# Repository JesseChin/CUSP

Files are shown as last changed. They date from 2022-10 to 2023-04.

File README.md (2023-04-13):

# CUSP

[github link](https://github.com/JesseChin/CUSP)

[User Guide](https://github.com/JesseChin/CUSP/blob/main/docs/User%20Guide.docx)

## Project Description

The Compact UAV Sensor Package (CUSP) is a low-cost camera sensor package with a longwave infrared (LWIR, 8 μm to 14 μm) and a high-resolution RGB camera for use with UAV remote sensing. The package is being developed as part of NASA Land Cover and Land Use Change and Ecosystems priority topic for NASA SERVIR-WA (West Africa) and for the Center for Remote Sensing and Geographic Information Services (CERSGIS), collaborating with the Environmental Protection Agency in Ghana. The purpose of these sensors is to combat deforestation and land degradation by monitoring illegal charcoal production and Galamsey operations (illegal small-scale gold mining). A machine learning model will be created to recognize these sites and report to the operator live.

CUSP is a unique low cost and lightweight product that provides on-board Machine Learning processing, a simple web configuration portal, and is fully open-source. Existing commercial solutions which provide live on-board image recognition do exist, though they are not open-source and certainly not budget-friendly. Existing open-source implementations, such as Imaging Package for Remote Vehicles (imPROV) do not provide ML capabilities, rely on 4G to operate, and occupy a large volume. CUSP is the only low-cost, small, and open-source sensor capable of monitoring illegal charcoal production and Galamsey.

---
## Screenshots

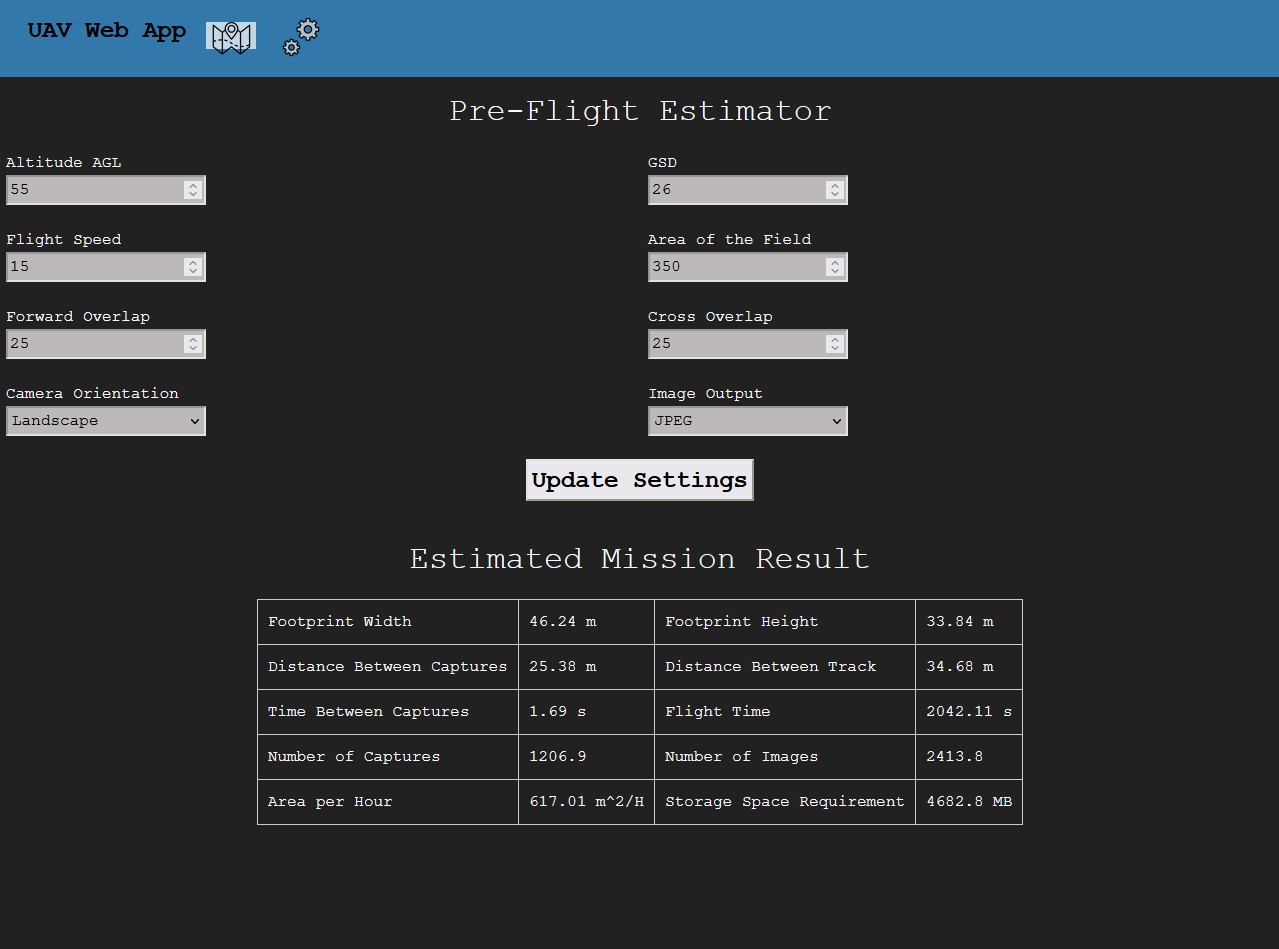
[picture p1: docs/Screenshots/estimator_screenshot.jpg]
estimator_screenshot


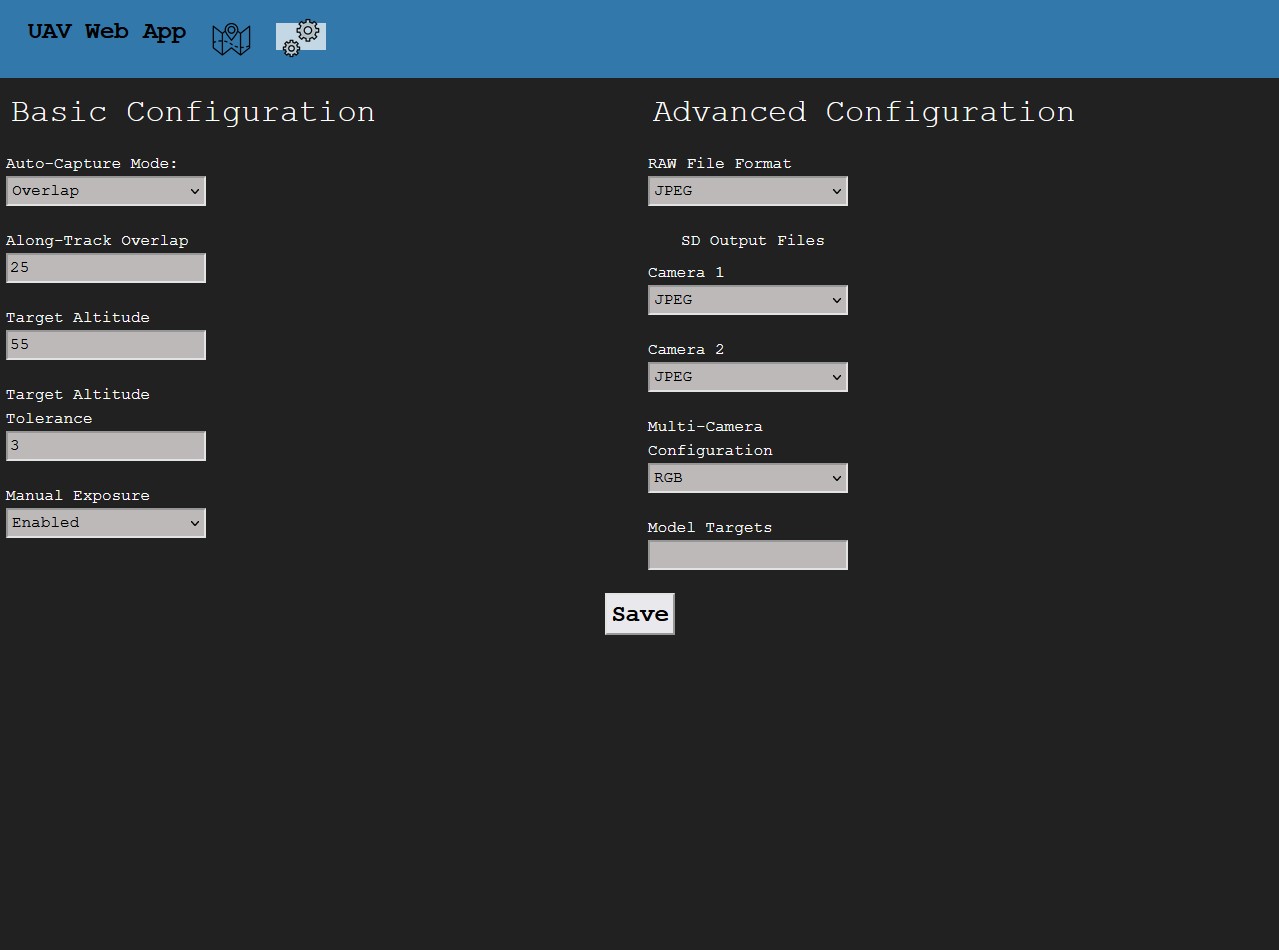
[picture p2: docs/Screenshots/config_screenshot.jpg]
config_screenshot


---
## Requirements

### Hardware
- Raspberry Pi 3/4
- MAVLink Capable Flight Controller
- 15-pin Raspberry Pi Compatible Camera
- FLIR Lepton Thermal Imaging Sensor
- CUSP Pi Hat
- 3D printed Chassis
- 4x M2.5x20 screws
- 9x M2.5x6 screws
- 4x M2x6 screws

### Software
- Python 3.9.2+
- Pymavlink
- Flask

---
## System Diagram

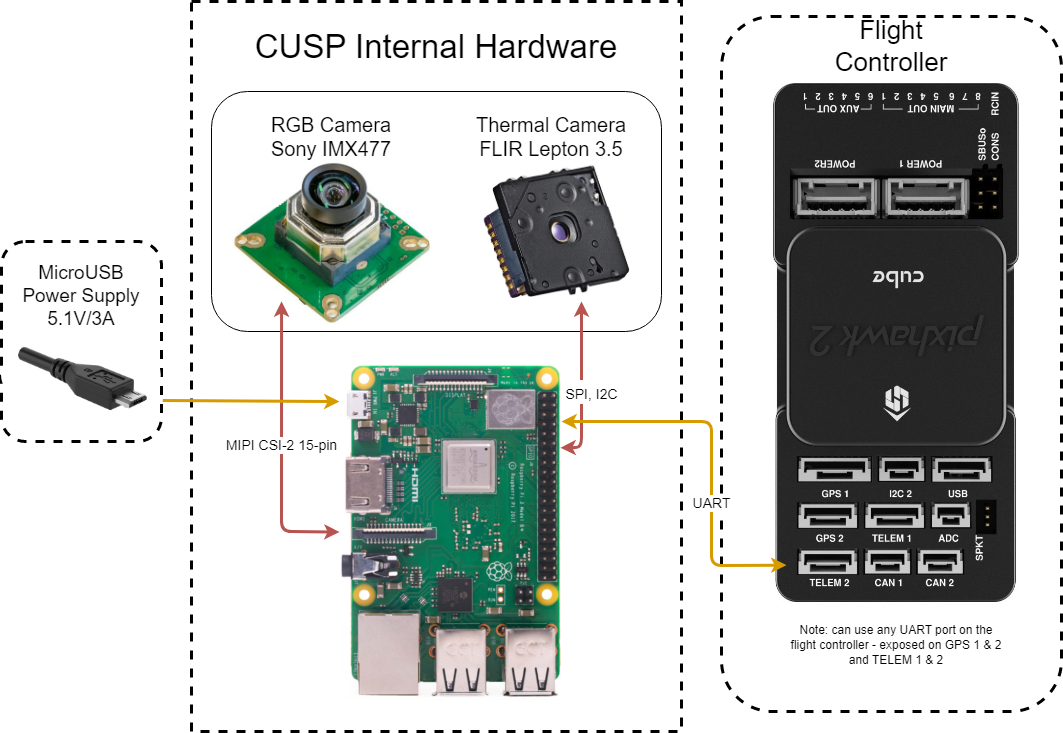
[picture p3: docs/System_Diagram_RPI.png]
System Diagram


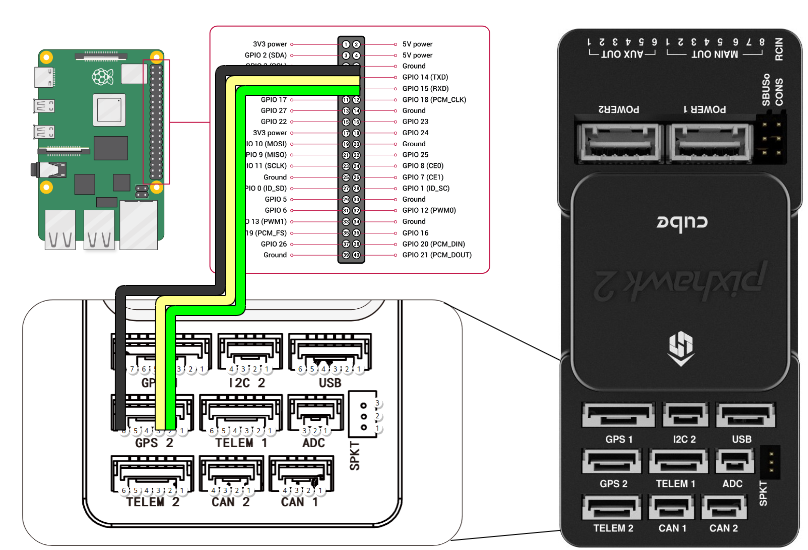
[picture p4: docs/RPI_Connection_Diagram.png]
Raspberry Pi <---> Flight Control


---
## Component Explanation

`MAVLINK_Camera` is a folder containing test scripts intended to run on the raspberry pi. `get_params_test.py` and `mavlink_test.py` tests the MAVLink connection and `camera_get.py` tests the attached camera. `CUSP_camera.py` is the camera capturing module, `CUSP_error_types.py` is the error type module, `CUSP_gps.py` is the gps handling module, `CUSP_messages.py` is the module containing our message enumerations, `CUSP_trigger.py` is the moduel containing logic for specific event triggers, and finally `main.py` is the application stating point.

captured images are saved in the `$HOME/data` directory on the pi.

The `Web_App` folder contains all the files needed to host the web server on the Raspberry Pi. The server is written in Python with Flask and HTML+CSS. the static folder contains all the assets and the templates folder contains all the html files. `app.py` is the starting point.

The `docs` folder will contain any extra documentation as the project develops. For example, `gcs_test_msg.PNG` and `gcs_test_msg1.PNG` show that `mavlink_test.py` is functional.

The `sim` folder contains all our files to help simualte a flight controller in flight so we do not need to actually fly a drone to develop new featues. Does not require running on hardware, can be fully simulated directly on a development machine. [This README](sim/README.md) contains much more info.

The `pi_sim` folder contains a mocked implementation of the GPS module and supports SITL running directly on the Pi for simulating a flight without actually flying the drone. The camera capturing mode here is fully implemented. This is where most of our development occurs.

### Persistent State

Camera capturing configuration parameters are stored in `$HOME/Web_App/form_data.json`. This json file contains the parameters for target altitude, target altitude tolerance, capturing mode (trigger, overlap, PWM), and output modes (JPEG, TIFF). Upon startup of the main application (`main.py`), this json is read. In the event of power loss, the camera configuration data is still held.

Images are saved into the `$HOME/images/` directory. Images are saved in the format YYYY_MM_DD_HH_MM_SS_{RGB, IR}. Currently, we are saving the IR images in RAW format for further radiometric processing.

---
## Setup
To use the Lepton sensor we needed to modify the kernel of the Pi. [This guide](https://github.com/FLIR/Lepton/blob/main/docs/RaspberryPiGuide.md) worked for us.

MAVProxy is a convenient way to test the connection of the Pi and flight controller. It also installs pymavlink as a dependency:
```
sudo apt-get install python3-dev python3-opencv python3-wxgtk4.0 python3-pip python3-matplotlib python3-lxml python3-pygame
pip3 install PyYAML mavproxy --user
echo 'export PATH="$PATH:$HOME/.local/bin"' >> ~/.bashrc
```

```
sudo apt install libimage-exiftool-perl libcamera
pip install PyExifTool
```

For autostarting the program:
```
sudo cp scripts/* /etc/systemd/system/
sudo systemctl enable cusp-main.service
sudo systemctl start cusp-main.service
sudo systemctl enable cusp-web.service
sudo systemctl start cusp-web.service
```

After that, installing Flask is simple:

```
pip install Flask flask-wtf flask-reuploaded
```

Now make sure the system is wired as shown in the [System Diagram](#System-Diagram), and you should be able to run our test scripts.

## Usage

to start the web server connect to the pi via SSH, navigate to the Web_App folder, and run the following command:

```
flask run --host=<ip_address>
```

Alternatively, the web server can also be called via `./scripts/run_webserver.sh`. This script automatically determines the ip of the pi.

where `<ip_address>` is replaced with the Pi's current ip address.

Once this is running you will be able to access the web interface through any web browser (we tested both Chrome and Firefox) by typing `http://<ip_address>:5000` into the address bar, once again replacing `<ip_address>` with the Pi's current ip address.

This whole process will hopefully be made much more user friendly in upcoming builds.

At this point there are two useful tabs, both of which can be accessed with the icons on the navigation bar on the top of the screen.

The first is the Pre-Flight Estimator. This tab allows the user to estimate the stats of a flight using already known variables. To learn the units of each variable, simply hover your mouse over it. When the user is ready they can select the large "Update Settings" button and they will either be greeted with an appropriate error message or the result of their flight.

The next useful tab is the Configuration Menu. This is where the data is configured for the actual flight. Once this data is filled the user can select the "Save" button, at which point they will receive a notification containing an appropriate error message or "JSON Saved"

We are using systemd services to run CUSP as a background process. Systemd supports automatically starting programs upon an operating system hook (i.e., network daemon activated) and restarting when an error occurs. If the systemd services are active, the main program and webserver should launch automatically on startup. Upon crash of either program, systemd should wait 5 seconds and auto-restart the service.

### Manual flight with pi_sim
pi_sim requires a connection to SITL. Because DroneKit-SITL does not have ARM builds, ardupilot SITL must be built manually using the [ArduPilot Building Guide](https://github.com/ArduPilot/ardupilot/blob/master/BUILD.md).

To begin a flight simulation, run the steps in [the sim README](sim/README.md).
After launching SITL, navigate to the pi_sim folder and run the following command:

```
python3 main.py
```

Now, images will be automatically captured dependent on the camera configuration. For example, if trigger capturing mode is enabled with a period of 10s, RGB and IR images will be captured every 10 seconds.

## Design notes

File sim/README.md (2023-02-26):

# Software Simulator

Software In The Loop (SITL) is a simulator that allows running ArduPilot without hardware. Using this, we are able to simulate running CUSP without having to connect to the flight controller and cameras.

There are two ways of running SITL: with the official ArduPilot codebase or using DroneKit-SITL. DroneKit-SITL does not have as many pre-built vehicles, but is significantly easier to install and run. In this project, we will be using DroneKit-SITL.

https://ardupilot.org/dev/docs/sitl-simulator-software-in-the-loop.html
https://dronekit-python.readthedocs.io/en/latest/develop/sitl_setup.html

To install DroneKit-SITL:
`pip install dronekit-sitl -UI`

To run DroneKit-SITL:
`dronekit-sitl copter`
SITL starts and waits for a TCP connection at 127.0.0.1:5760

Using SITL instead of a UART connection to MAVLink is quite easy, just a drop-in replacement in the Python code.

Connection with UART on a Raspberry Pi to a Flight Controller:
```
...
    the_connection = mavutil.mavlink_connection('/dev/serial0', baud=57600, source_system=1, source_component=2)
...
```

Connection with SITL
```
...
    the_connection = mavutil.mavlink_connection('tcp:127.0.0.1:5760', baud=57600, source_system=1, source_component=2)
...
```

## Example of running a simulation

Process to manually test a simulated flight:
Activate SITL process 
```
cd ~/ardupilot/ArduCopter
../Tools/autotest/sim_vehicle.py --map --console
```
OR
```
dronekit-sitl copter --home=-35.363261,149.165230,584,353 # Can change coords
```
Connect to SITL with MAVProxy. Open a new terminal and run,
```
mavproxy.py --master tcp:127.0.0.1:5760
```
Add MAVLink output so that we can connect another application to SITL. In terminal running MAVProxy:
```
output add 127.0.0.1:14550
```
Connect to MAVProxy with our application via address udp:127.0.0.1:14550
Run flight. This simulated flight takes the drone to 40m, and flies in a 2000m circle. In MAVProxy terminal:
```
mode guided
arm throttle
takeoff 40
mode circle
param set circle_radius 2000
```

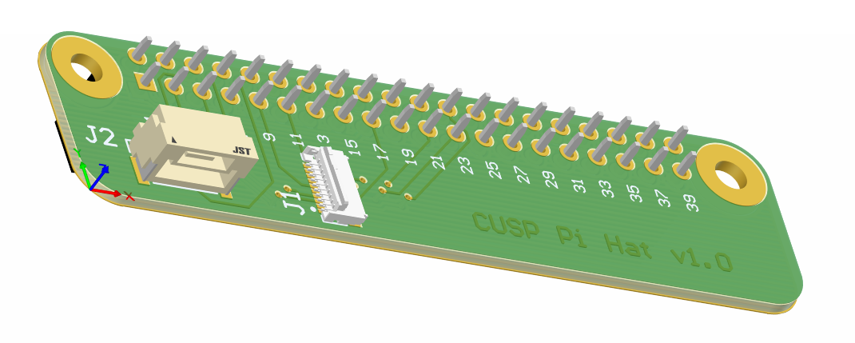
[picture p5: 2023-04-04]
hardware/Pi Hat.png

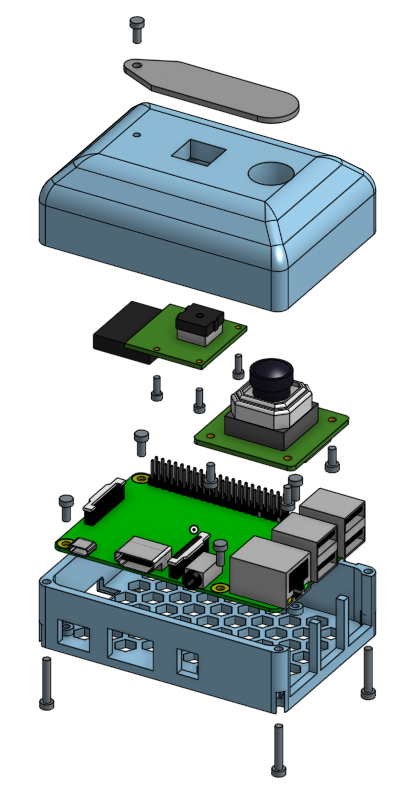
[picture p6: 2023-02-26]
hardware/explosion_view.png

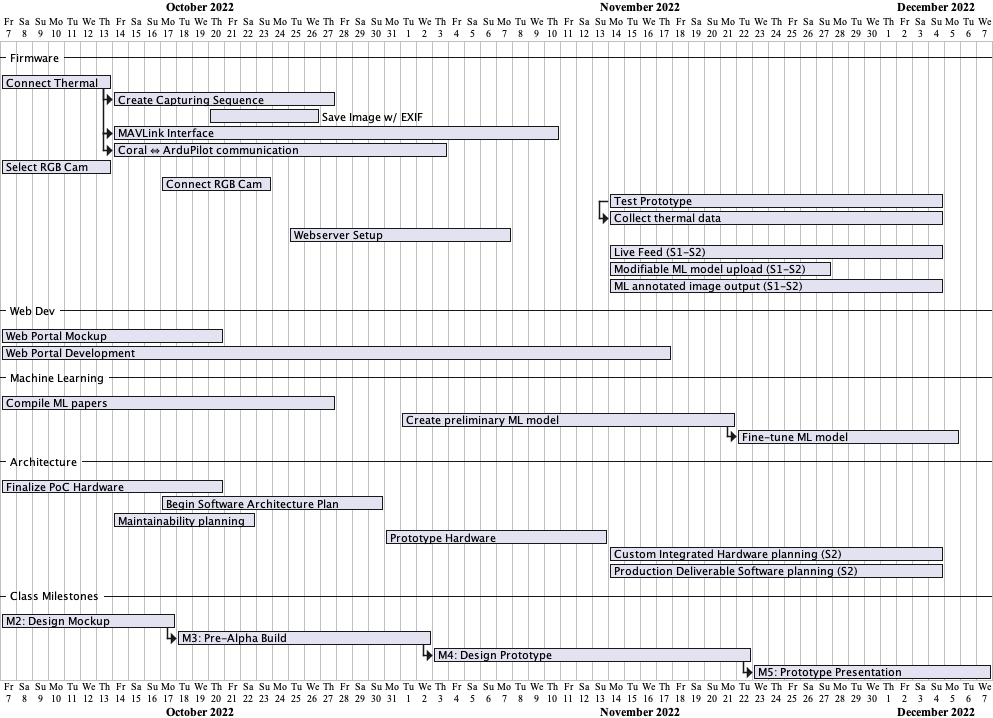
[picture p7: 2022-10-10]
out/plantuml/GanttChartSemester1/GanttChartSemester1.png

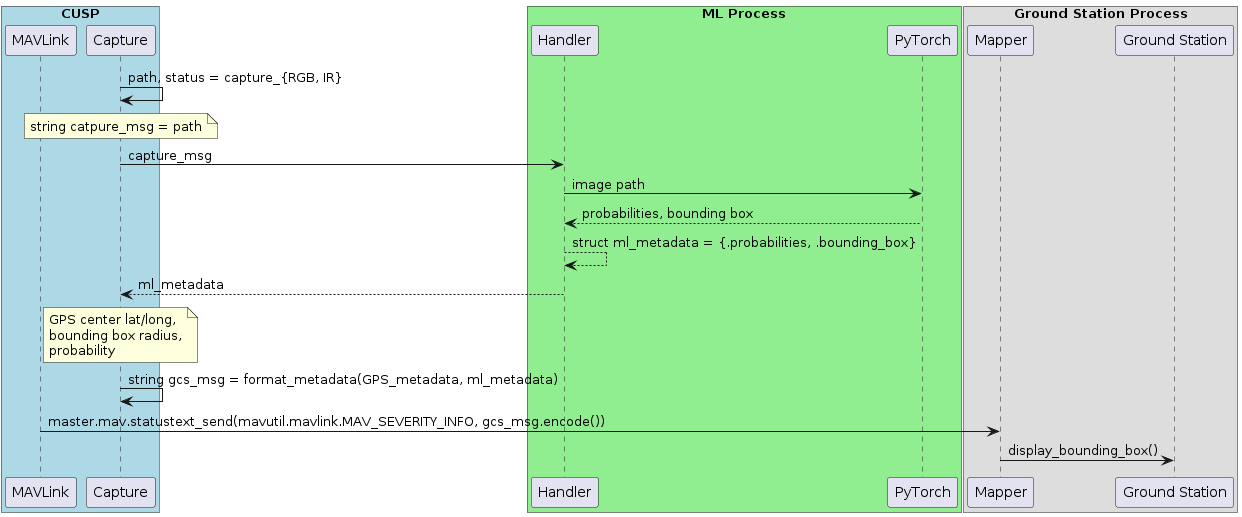
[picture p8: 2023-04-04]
out/plantuml/ML_Integration.png

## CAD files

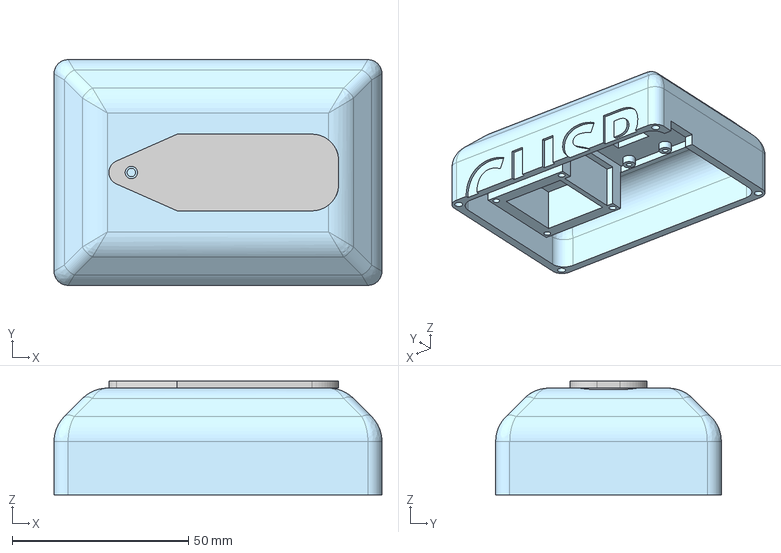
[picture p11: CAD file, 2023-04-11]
hardware/Case/Top Shell.step
93.0 x 64.0 x 32.3 mm

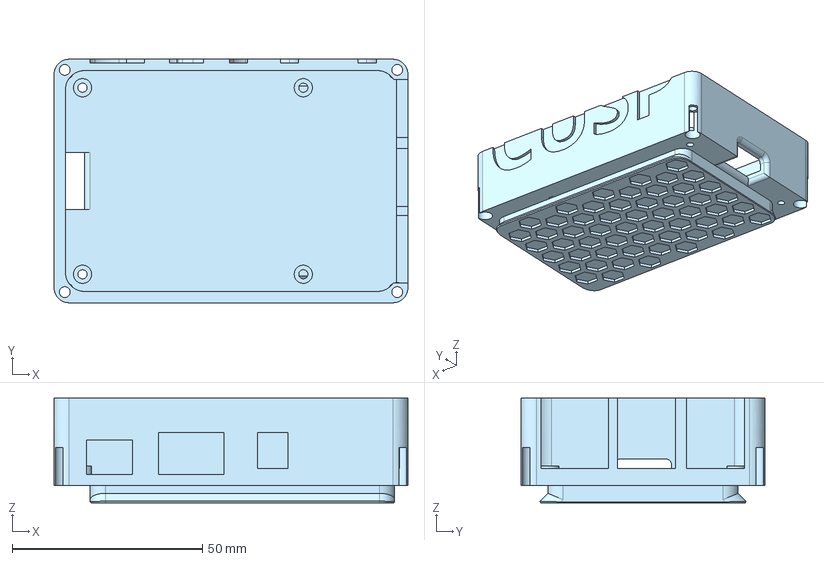
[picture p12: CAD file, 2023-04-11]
hardware/Case/Bottom Shell.step
93.0 x 64.0 x 27.5 mm

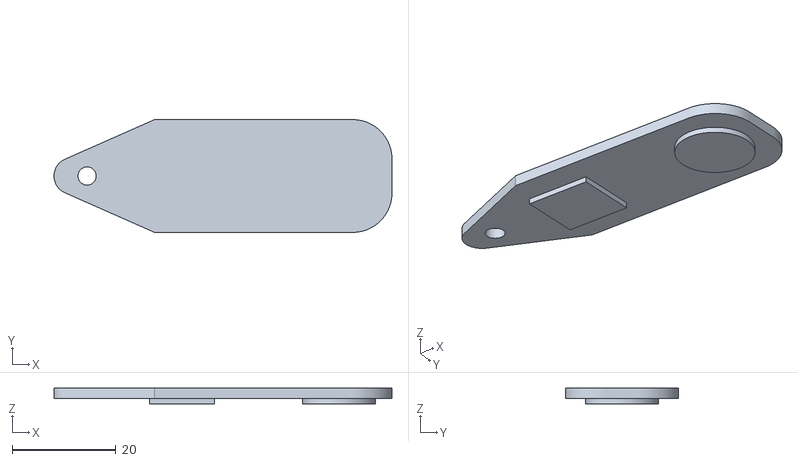
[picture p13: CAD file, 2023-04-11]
hardware/Case/Lens Cover.stl
65.2 x 21.7 x 3.00

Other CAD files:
hardware/Case/Bottom Shell.stl
hardware/Case/Top Shell.stl

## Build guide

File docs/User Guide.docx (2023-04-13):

1. Power CUSP via microUSB (or USB-C if using a RPi 4).
2. Once Cusp is powered, a wireless ad hoc network will be generated called “CUSP-XXX” where XXX will denote the unit number.
3. A user can then connect to this network just like any WiFi network using the password which is given upon arrival.
4. Upon connection, the user can now access the web app.

Web App

Go to the address 192.168.4.1:500 in a web browser.

This should bring you to the Home Page.

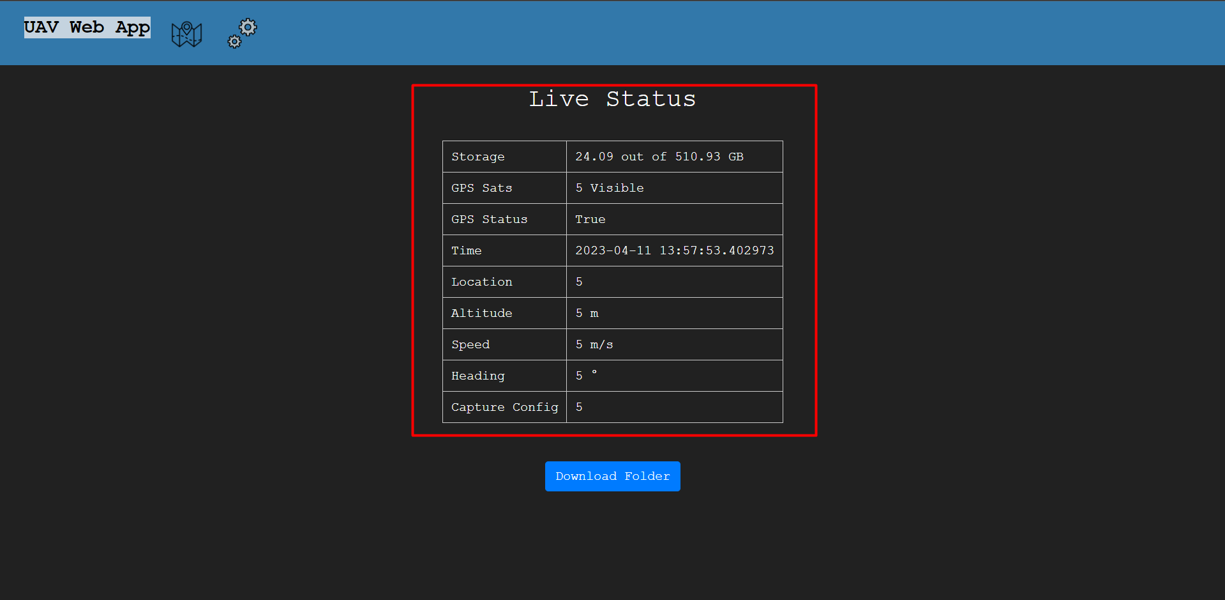
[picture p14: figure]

This part of the home page displays the status of the gps in real time.

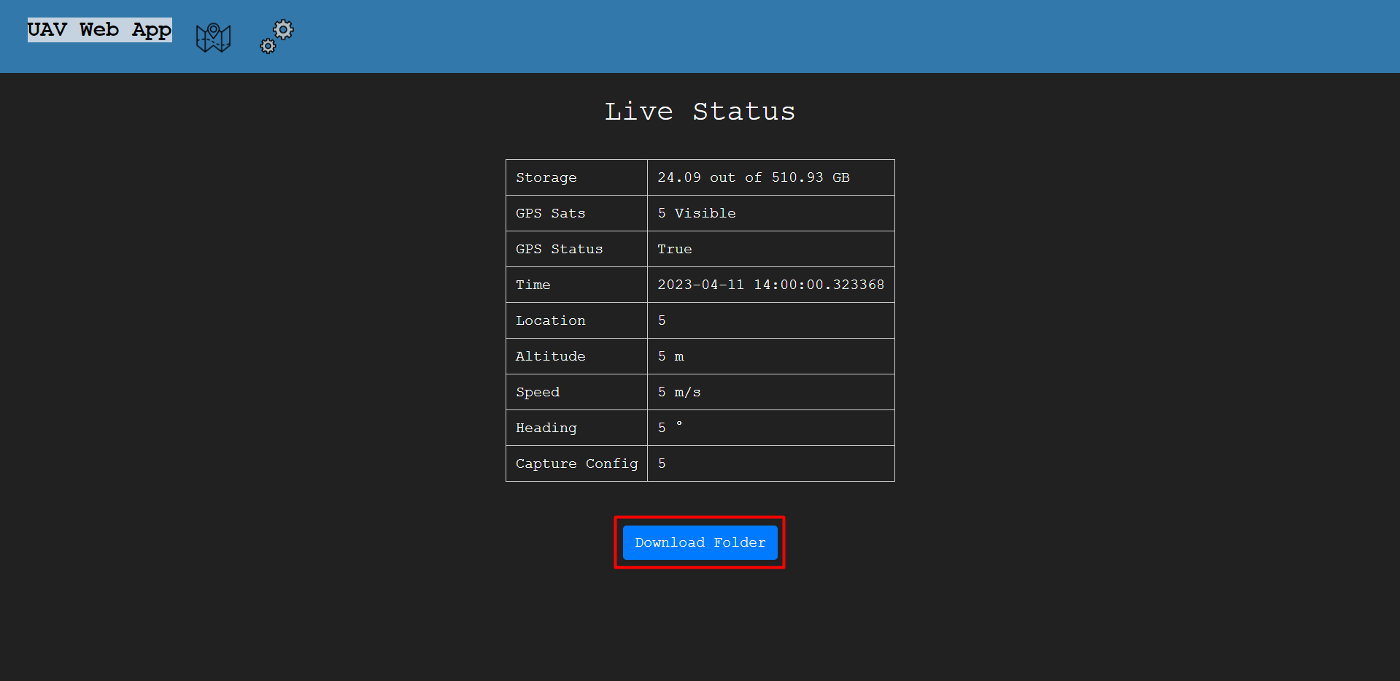
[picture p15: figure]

This button allows you to download a zipped folder of the images taken.

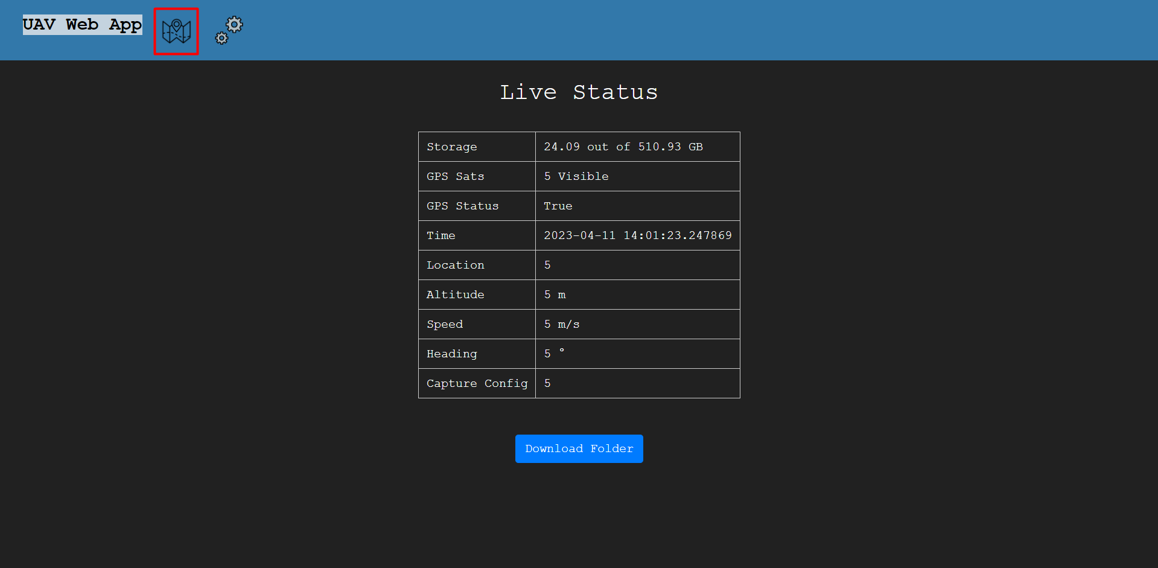
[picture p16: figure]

There are 3 tabs in the navigation bar at the top of the screen. This one will bring you to the Flight Estimator page.

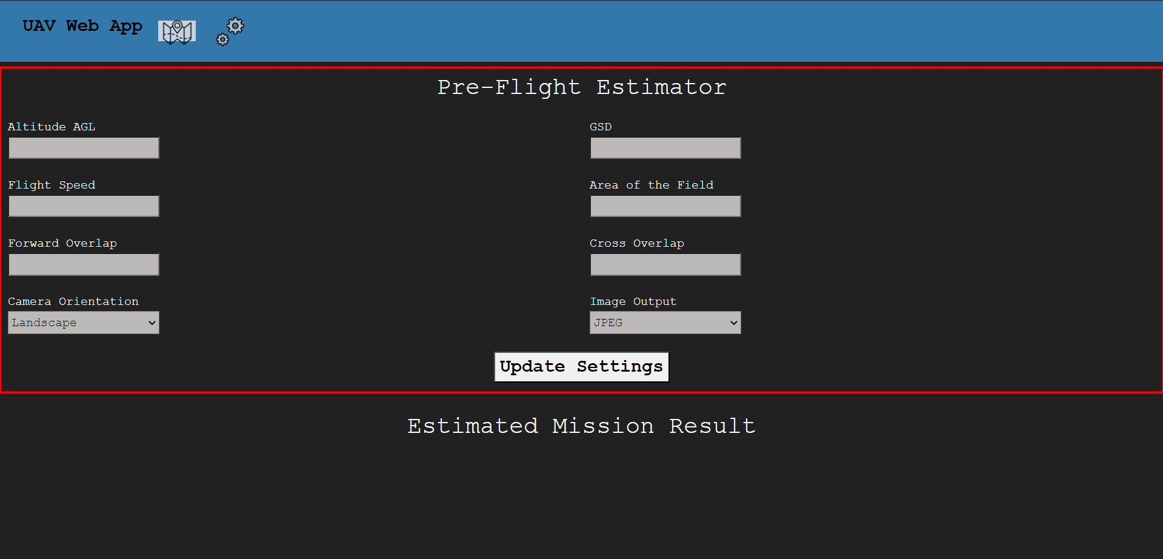
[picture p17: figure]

This section of the Flight Estimator page is where you input the values.

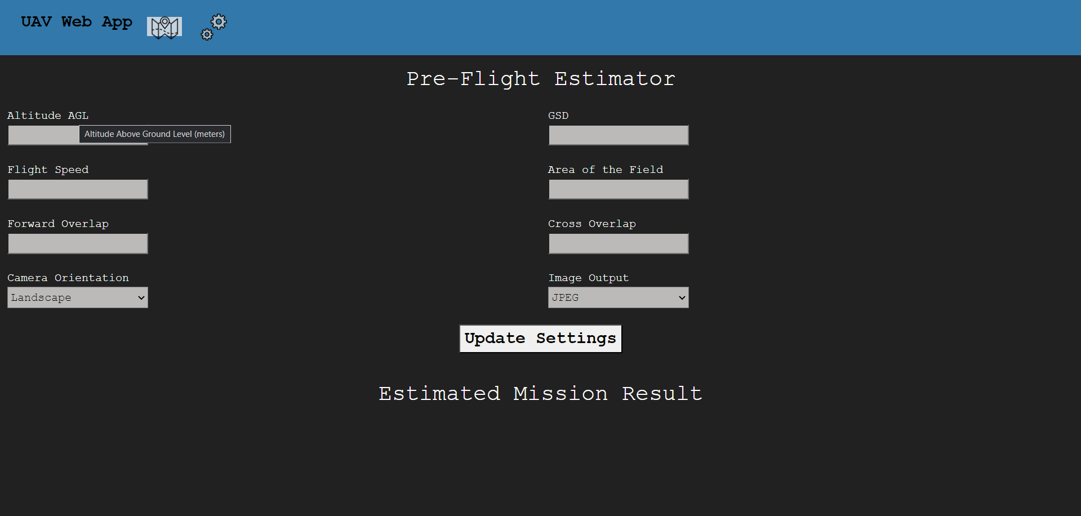
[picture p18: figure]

Hovering over any of the values will give you a description of what to input.

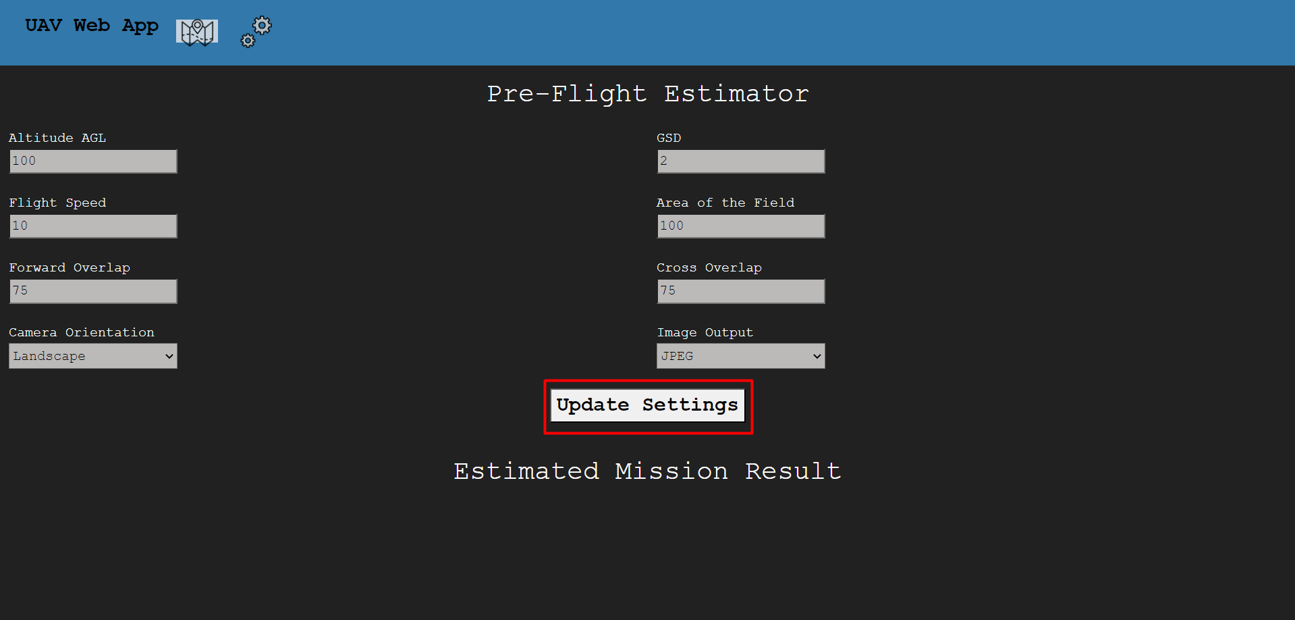
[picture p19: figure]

After entering your chosen values this button will perform the calculations.

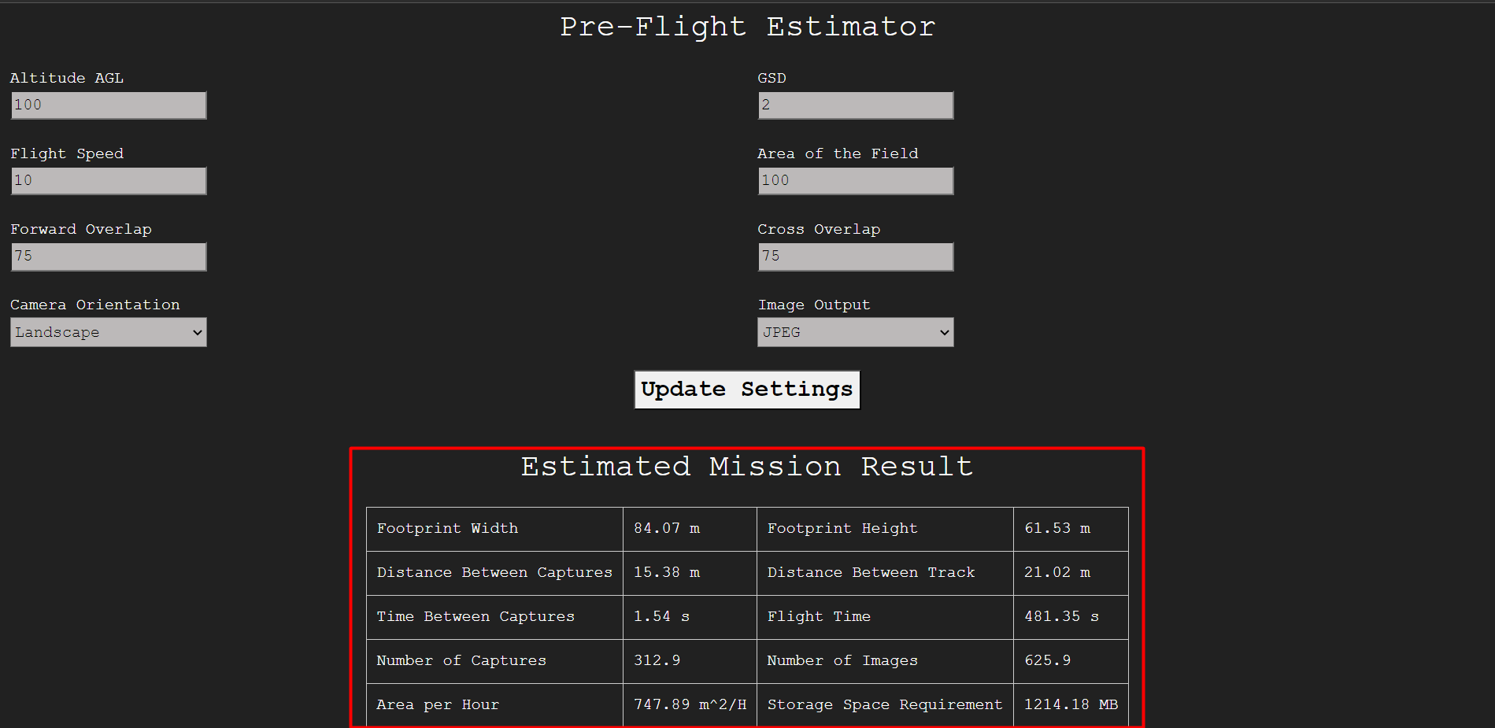
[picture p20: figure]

After clicking the button, the estimated mission result is shown here.

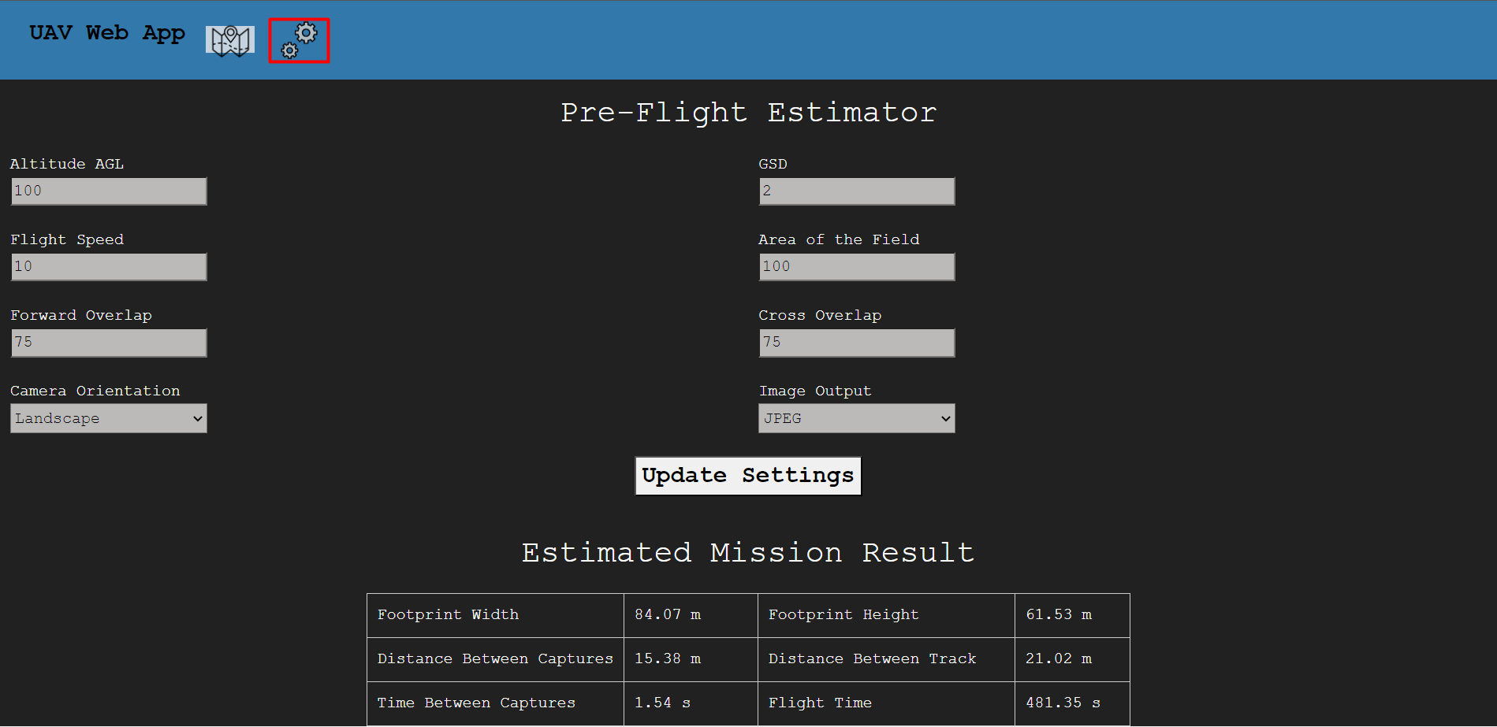
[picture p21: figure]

Heading back up to the navigation bar, this tab will bring you to the configuration page.

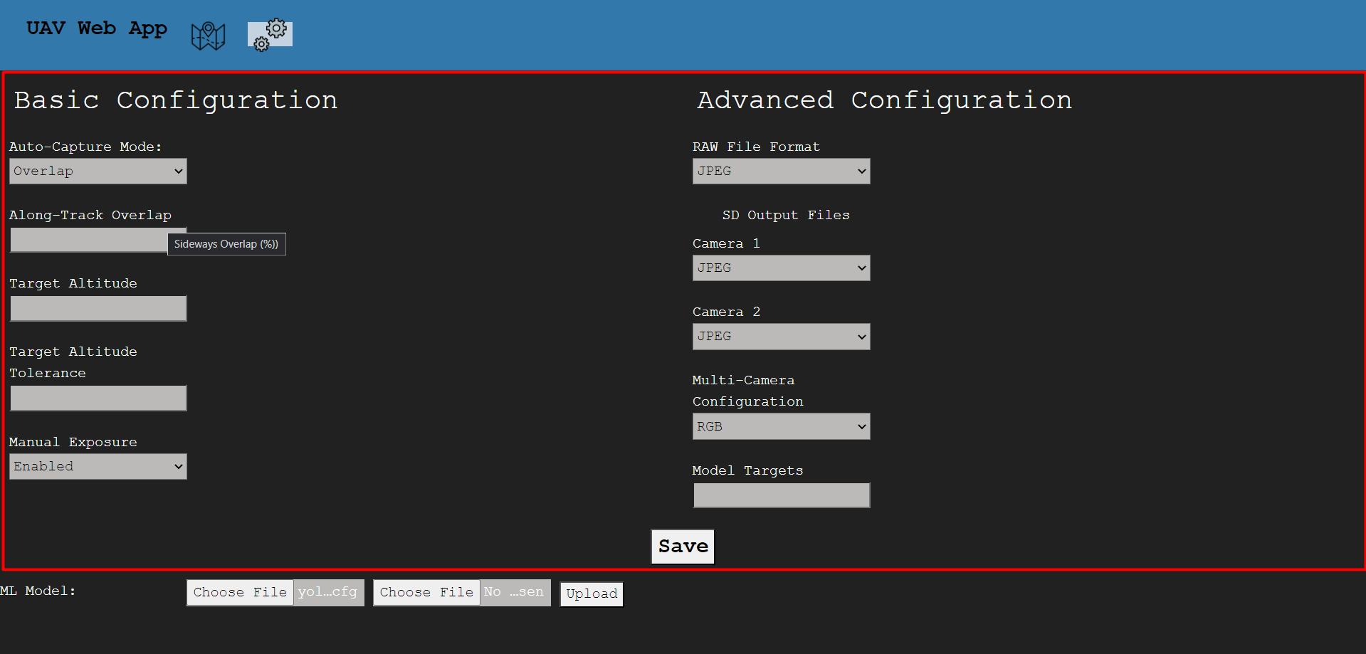
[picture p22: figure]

This is the configuration section. This also has the hovering ability to show a description of what the setting means. Model Targets does not have to be filled out to submit a configuration change.

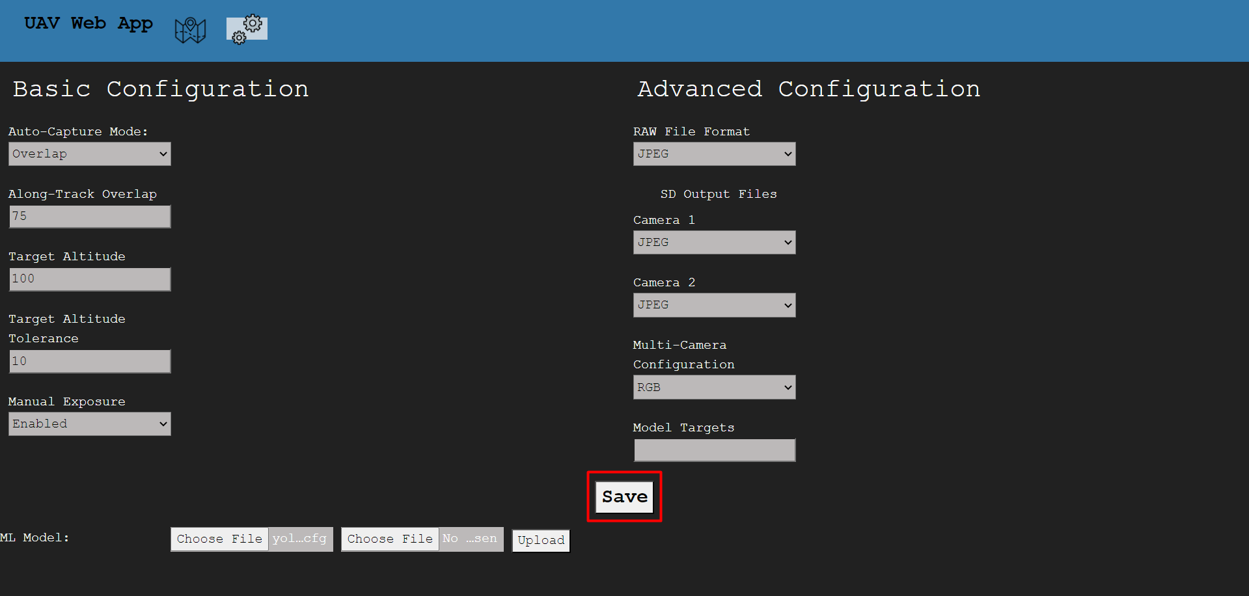
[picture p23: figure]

Upon entering desired configuration settings, this button will upload those settings.

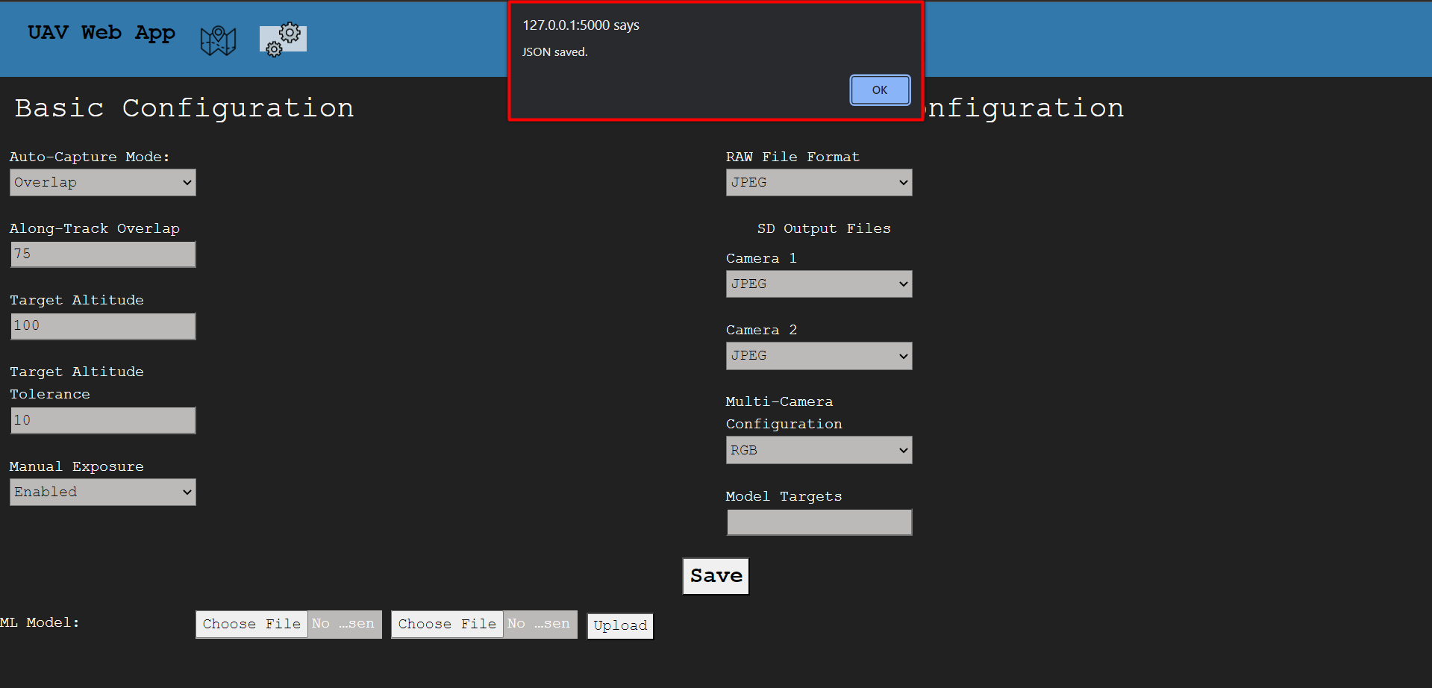
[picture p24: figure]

If successful, this message will pop up.

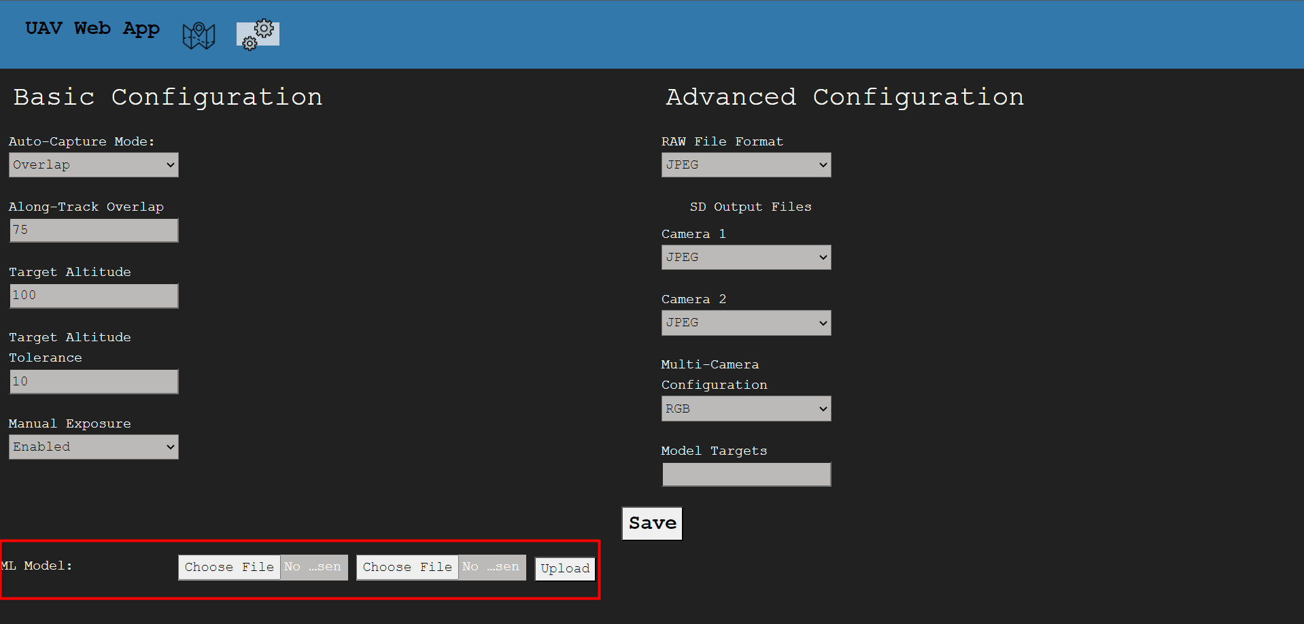
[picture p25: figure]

This section allows for the uploading of updated or new machine learning models.

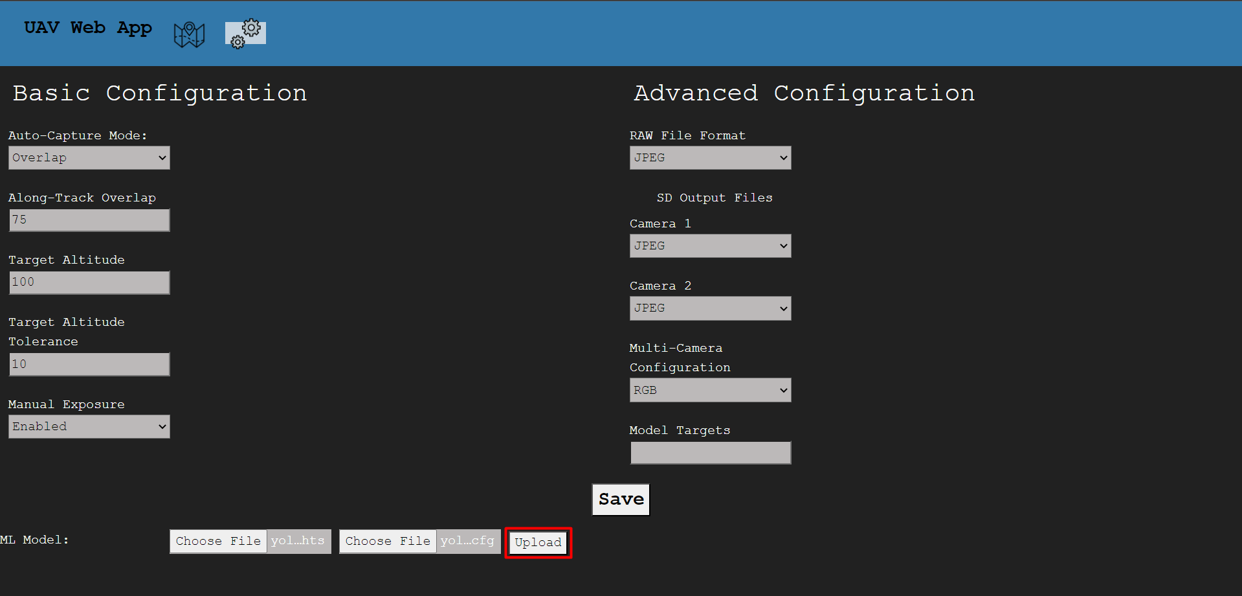
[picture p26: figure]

After choosing the .cfg and the .weights file, this button will upload the models.

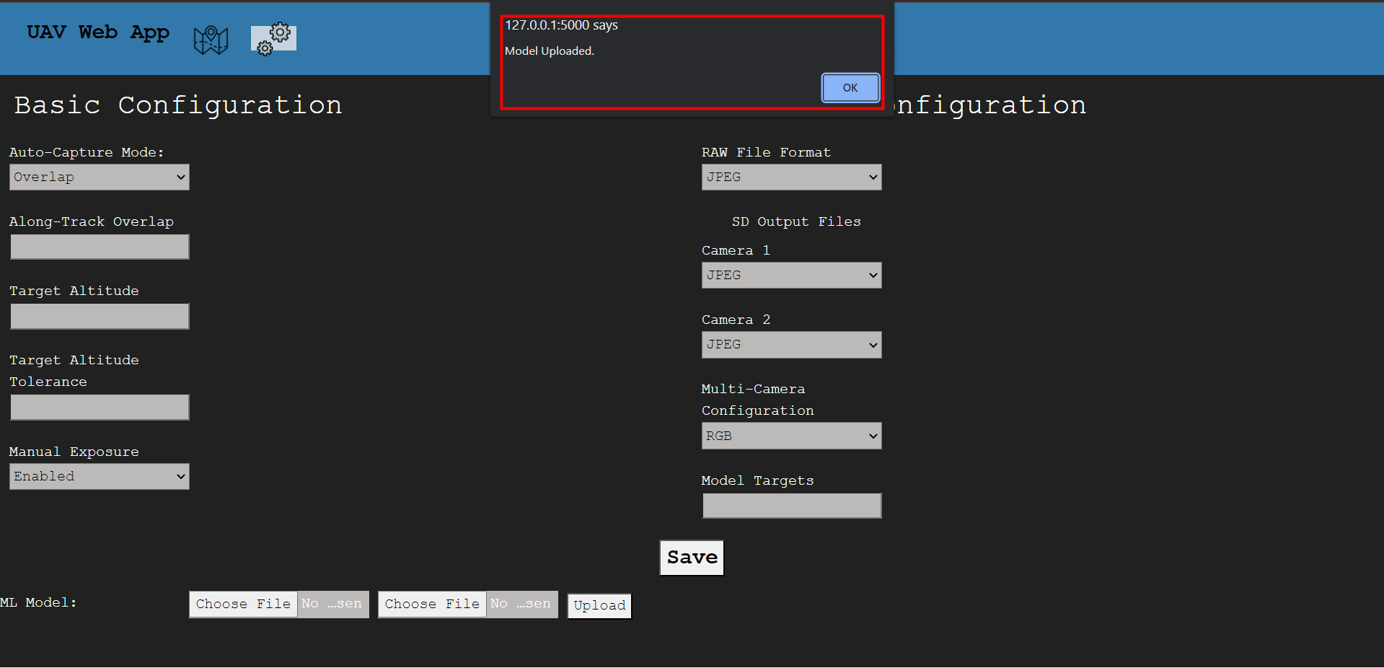
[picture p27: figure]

Upon successful upload, this message will pop up.

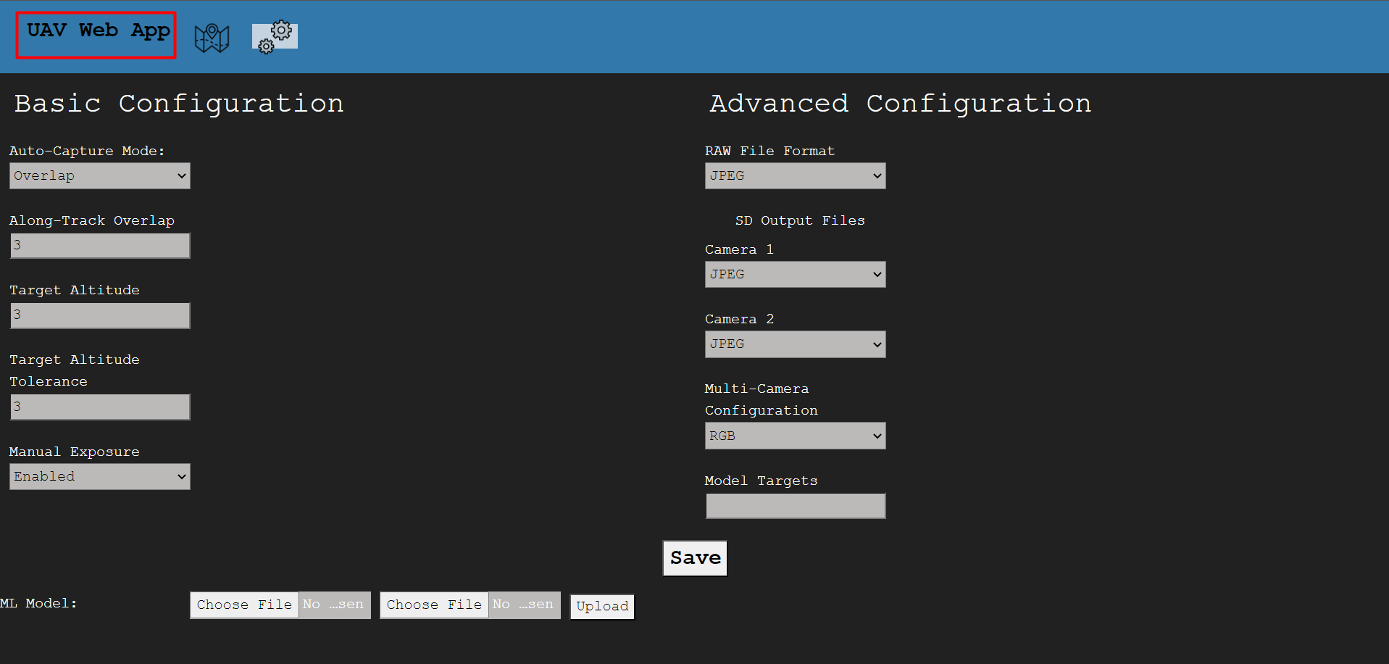
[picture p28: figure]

Lastly, this tab in the navigation bar will bring you to the home page.

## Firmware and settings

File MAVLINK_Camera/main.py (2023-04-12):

#!/usr/bin/env python3

from typing_extensions import get_args
from pymavlink import mavutil
import time
import sys
from CUSP_camera import *
from CUSP_trigger import *
from CUSP_gps import *
from camera_definitions import *
import json
import math
import random

# from multiprocessing import Process
from threading import Thread, Lock
import queue
import grpc
import os, sys

import pickle

sys.path.append(
    os.path.join(os.path.dirname(__file__), "../rt-flight/raspberry_pi_code/protos")
)
import messaging_pb2
import messaging_pb2_grpc

"""
Main program to run CUSP
Handles all MAVLink communication here
"""

LEPTON_HFOV = float(flir_lepton_3_5["DiagFOV"])*float(flir_lepton_3_5["XResolution"])/math.sqrt(float(flir_lepton_3_5["XResolution"])**2 + float(flir_lepton_3_5["YResolution"])**2)
LEPTON_VFOV = float(flir_lepton_3_5["DiagFOV"])*float(flir_lepton_3_5["YResolution"])/math.sqrt(float(flir_lepton_3_5["XResolution"])**2 + float(flir_lepton_3_5["YResolution"])**2)

msg_buffer = queue.Queue()


def poll_GPS(periodSeconds, GPS, the_connection):
    # Handle polling GPS data here

    # Initial GPS run for setting home altitude
    the_connection.wait_gps_fix()

    while True:
        msg = the_connection.recv_match(type="GPS_RAW_INT", blocking=True)
        GPS.set_GPS_data_RAW_INT(msg)

        msg = the_connection.recv_match(type="ATTITUDE", blocking=True)
        GPS.set_GPS_data_ATTITUDE(msg)

        msg = the_connection.recv_match(type="GLOBAL_POSITION_INT", blocking=True)
        GPS.set_GPS_rel_height(msg)

        # might have to bump up frequency depending on how fast it's flying
        with open("gps.pkl", "wb") as f:
            pickle.dump(GPS, f)
        sleep(periodSeconds)


def process_path_buffer(msg_buffer, the_connection):
    channel = grpc.insecure_channel("localhost:50951")
    stub = messaging_pb2_grpc.MessagingServiceStub(channel)
    while True:
        item = msg_buffer.get(block=True)
        # Write item to GRPC so that the model can see
        # Print path sending as a test
        print("Sending path: ", item)
        response = stub.GetBoundingBoxes(messaging_pb2.File_Payload(path=item))
        print("Sending to GCS: ", response.bboxes)
        # print(response.status)
        the_connection.mav.statustext_send(
            mavutil.mavlink.MAV_SEVERITY_NOTICE, str(response.bboxes).encode()
        )
        sleep(1)


def startTrigger(trigger):
    while True:
        trigger.trigger_loop()


def main():

    # Activate connection to flight controller

    master = mavutil.mavlink_connection(
        "udp:127.0.0.1:14550", baud=57600, source_system=1, source_component=2
    )
    print("Creating connection...")

    master.wait_heartbeat()
    print(
        "Heartbeat from system (system %u component %u)"
        % (master.target_system, master.target_component)
    )

    GPSprocess = Thread(target=poll_GPS, args=(0.1, GPS_dev, master,),)
    GPSprocess.start()

    ModelSenderProcess = Thread(target=process_path_buffer, args=(msg_buffer, master,))
    ModelSenderProcess.start()

    # Wait until GPS receives data
    # while any(v is None for v in GPS_dev.get_GPS_data()):
    while GPS_dev.get_GPS_data() is None:
        print("Waiting for GPS uplink")
        sleep(1)

    lat_start, long_start, alt_start = GPS_dev.get_GPS_data()

    configJSON = open("../Web_App/form_data.json")
    configData = json.load(configJSON)
    configData = json.loads(configData)
    print("JSON loaded")
    # update trigger mode
    if configData["acmode"] == "Periodic":
        trigger = Trigger_Timer(msg_buffer, 15)
        trigger.deactivate_trigger()
        triggerProcess = Thread(target=startTrigger, args=(trigger,))
        triggerProcess.start()
    elif configData["acmode"] == "Overlap":
        trigger = Trigger_Overlap(msg_buffer)
        trigger.set_GPS(GPS_dev)
        trigger.set_fov(LEPTON_VFOV)
        trigger.set_stating_altitude(alt_start)
        trigger.set_overlap_percent(int(configData["along-track_overlap"]))
        trigger.deactivate_trigger()
        triggerProcess = Thread(target=startTrigger, args=(trigger,))
        triggerProcess.start()
    # elif (configData['acmode'] == "PWM"):
    #     trigger = Trigger_PWM()
    altitude_target = configData["target_altitude"]
    altitude_tolerance = configData["target_altitude_tolerance"]

    tick = 0
    while True:

        latitude, longitude, altitude = GPS_dev.get_GPS_data()

        if float(altitude_target) > altitude - float(altitude_tolerance) and float(
            altitude_target
        ) < altitude + float(altitude_tolerance):
            trigger.activate_trigger()
            print(f"Altitude within tolerance: {altitude}")
        else:
            trigger.deactivate_trigger()
            print(f"Altitude outside tolerance: {altitude}")

        sleep(1)
        tick += 1


if __name__ == "__main__":
    main()

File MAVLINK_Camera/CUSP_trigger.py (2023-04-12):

#!/usr/bin/env python3
"""
Capturing modes for CUSP
Currently working on: PWM and Overlap
MAVLink Camera Protocol not supported yet
"""

from CUSP_camera import *
from math import sin, cos, tan, asin, acos, atan, pi, atan2, sqrt

# import RPi.GPIO as GPIO
# Use apigpio instead as it has asyncio support
from time import sleep
from threading import Thread, Lock
from datetime import datetime

from multiprocessing import Process

import queue


class Trigger_Timer:
    """
    When activated, turn on trigger on each period
    """

    def __init__(self, msg_buffer, period=15):
        self.periodSeconds = period
        self.active = False
        self.triggerMutex = Lock()
        self.msg_buffer = msg_buffer

    def set_period(self, seconds):
        self.periodSeconds = seconds

    def set_frequency(self, Hz):
        self.periodSeconds = 1 / Hz

    def trigger_loop(self):
        with self.triggerMutex:
            if self.active:
                startTime = time.time()

                dt = datetime.now()
                filepath = "/home/sixth/images/" + dt.strftime("%Y-%m-%d_%H-%M-%S")
                print("Capturing RGB")
                retcode = capture_rgb_path(filepath + "_RGB.jpg")
                if retcode == Error.NO_ERROR:
                    self.msg_buffer.put(filepath + "_RGB.jpg")
                print("Capturing IR")
                retcode = capture_thermal_path(filepath + "_IR")
                if retcode == Error.NO_ERROR:
                    print("Adding IR path to buffer")
                    self.msg_buffer.put(filepath + "_IR.tiff")

                now = time.time()
                waitTime = self.periodSeconds - (now - startTime)
                print(
                    f"took {round(now - startTime,1)}s. waiting {round(waitTime,1)}s for next capture"
                )
                if waitTime < 0.1:
                    waitTime = 0.1
                sleep(waitTime - 0.1)
        sleep(0.1)

    def activate_trigger(self):
        with self.triggerMutex:
            self.active = True

    def deactivate_trigger(self):
        with self.triggerMutex:
            self.active = False


class Trigger_PWM:
    """
    Trigger capturing image upon receiving a HIGH PWM signal
    Implemented as a singleton
    """

    _instance = None

    def __new__(cls, *args, **kwargs):
        if not cls._instance:
            cls._instance = super().__new__(cls, *args, **kwargs)
        return cls._instance


def PWM_callback():
    return


def PWM_init():
    """
    Set up PWM GPIO and inialize callback function
    """
    return


class Trigger_Overlap:
    """
    Trigger capturing image upon receiving a HIGH PWM signal
    Implemented as a singleton
    """

    active = False
    triggerMutex = Lock()

    gpsObject = None
    fov = 42.6  # vertical lepton FOV
    alt_start = 0
    overlap_percent = 25

    lat_prev, long_prev, alt_prev = 0, 0, 0

    def __init__(self, msg_buffer):
        self.active = False
        self.triggerMutex = Lock()
        self.msg_buffer = msg_buffer

    def set_GPS(self, gpsObject):
        self.gpsObject = gpsObject

    def set_fov(self, fov):
        self.fov = fov

    def set_stating_altitude(self, alt_start):
        self.alt_start = alt_start

    def set_overlap_percent(self, overlap_percent):
        self.overlap_percent = overlap_percent

    def trigger_loop(self):

        with self.triggerMutex:
            if self.active:

                lat_now, long_now, alt_now = self.gpsObject.get_GPS_data()

                R = 6371
                lat_prev_r = self.lat_prev * pi/180
                lat_now_r = lat_now * pi/180
                dLat = (lat_now-self.lat_prev) * pi/180
                dLong = (long_now-self.long_prev) * pi/180

                a = sin(dLat/2) * sin(dLat/2) + cos(lat_prev_r) * cos(lat_now_r) * sin(dLong/2) * sin(dLong/2)
                distance_m = 1000 * R * 2 * atan2(sqrt(a), sqrt(1-a))

                distance_target_m = ((100 - self.overlap_percent) / 100.0) * 2 * (alt_now - self.alt_start) * tan(self.fov / 2)

                print(f"Distance traveled: {distance_m}m\nDistance target: {distance_target_m}m")

                if distance_m > distance_target_m:
                    self.lat_prev, self.long_prev, self.alt_prev = lat_now, long_now, alt_now
                    dt = datetime.now()
                    filepath = "/home/sixth/images/" + dt.strftime("%Y-%m-%d_%H-%M-%S")
                    print("Capturing RGB")
                    retcode = capture_rgb_path(filepath + "_RGB.jpg")
                    if retcode == Error.NO_ERROR:
                        self.msg_buffer.put(filepath + "_RGB.jpg")
                    print("Capturing IR")
                    retcode = capture_thermal_path(filepath + "_IR")
                    if retcode == Error.NO_ERROR:
                        print("Adding IR path to buffer")
                        self.msg_buffer.put(filepath + "_IR.tiff")
                else:
                    print("No Capture")
                    sleep(0.2)

    def activate_trigger(self):
        with self.triggerMutex:
            self.active = True

    def deactivate_trigger(self):
        with self.triggerMutex:
            self.active = False


def Overlap_init():
    """
    Set up Overlap triggering mode
    """
    return

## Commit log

2023-01-26 Rudimentary state machine style for the script, next thing to implement is reacting to camera capture requests
2023-01-27 removed switch statement for python 3.9.2
2023-01-27 added camera_get script
2023-02-18 Revert to Current
2023-02-21 made buttons bigger
2023-02-23 increased minimum wall thickness from ~0.4mm to ~0.8mm
    [Bottom Shell.step, Top Shell.step]
2023-02-23 updated timer trigger
2023-02-23 pi sim camera module rgb fix
    [CUSP_camera.py]
2023-02-23 moved gps polling to its own thread
2023-02-23 fixes for rgb cam
    [CUSP_camera.py]
2023-02-23 reverted breaking GPS_dev change
    [main.py, mock_gps.py]
2023-02-26 updated hardware
    [Bottom Shell.step, Top Shell.step]
2023-03-24 Pi hat 1.0 included
    [Bottom Shell.step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]
2023-03-26 added i2c to PCB, and reversed ports for debug
    [CUSP_PI_Hat.GBL, CUSP_PI_Hat.GBO, CUSP_PI_Hat.GBS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]
2023-04-02 experimental i2c gps support
2023-04-04 Added Model Upload Button
2023-04-05 updated case to include mount
    [Bottom Shell.step, Bottom Shell.stl, Lens Cover.stl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]
2023-04-06 Download Button Added
2023-04-10 gave more clearance to RGB cam to reduce vignette
    [Lens Cover.stl, Top Shell.step, Top Shell.stl]
2023-04-11 adjusted ribbon cable clearance
    [Lens Cover.stl, Top Shell.step, Top Shell.stl]
2023-04-11 added passthrough for wires
    [Bottom Shell.step, Bottom Shell.stl, Top Shell.step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]
2023-04-12 fixed Overlap mode not starting
    [CUSP_trigger.py, main.py]
2023-04-12 main.py now reads FOV from camera_definitions.py
2023-04-12 Added Prototypes
2023-04-12 added extra print info to overlap operation
